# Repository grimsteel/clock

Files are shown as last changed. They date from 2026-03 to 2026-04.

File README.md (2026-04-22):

# Clock

> Working 4-person location clock. Uses Home Assistant location zone information.

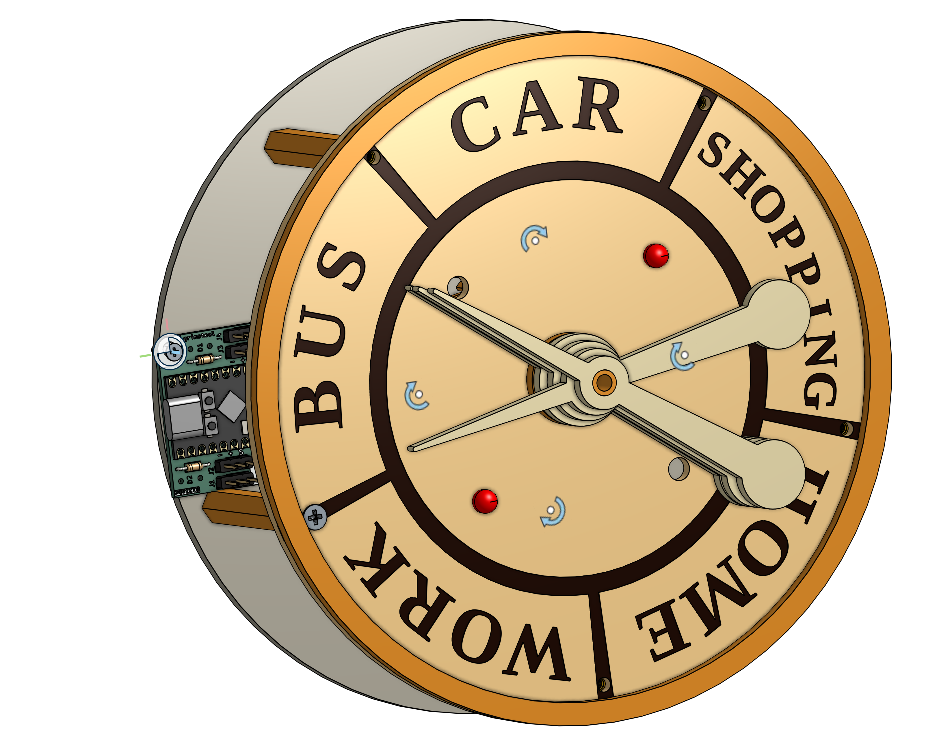
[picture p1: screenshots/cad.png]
CAD render


## Usage

### Assembly

1. 3D-print and laser cut the necessary components (see the `cad/` folder for a parts list and Onshape link)
2. Solder the ESP32 and pin headers onto the PCB.
3. Assemble the back frame (back, PCB, standoffs, and servo mount)
4. Attach the servos to the servo mount
5. Add the shafts, placing PTFE washers in between
6. Attach the front frame
7. Attach the front decorations and the hands

### Using it

8. Install one of the provided firmwares, configuring the people/locations as necessary (see `firmware/README.md`)
9. Profit. This does rely on accurate zone information in Home Assistant.

## Technical Information

### Structure

More information can be found in the `cad/` folder. The clock consists of a laser cut front and back frame.

Each hand is controlled by a servo with a 2:1 gear ratio. The servos and gears are mouted on a 3d-printed frame, which is fastened to the back frame.

The hands are attached to four concentric shafs, each terminating at a different height. This is part of the reason the clock is so thick.

The front includes 4 possible mounting spots for LEDs.

### PCB

The PCB consists of a surface mounted ESP32 C3 Supermini with connections for the 4 servos and 2 LEDs:

| Schematic | 3D render |
|---|---|
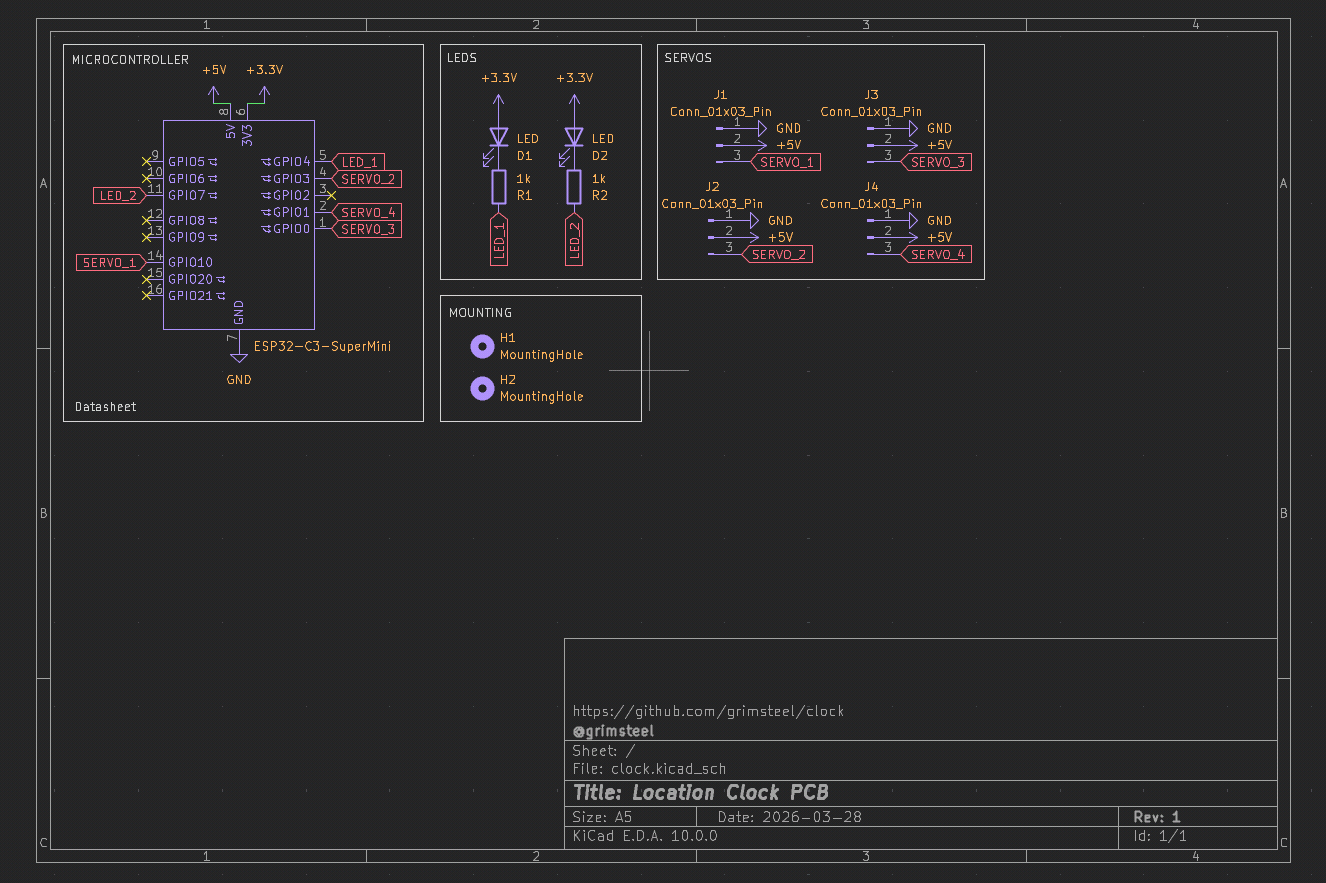
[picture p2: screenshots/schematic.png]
schematic
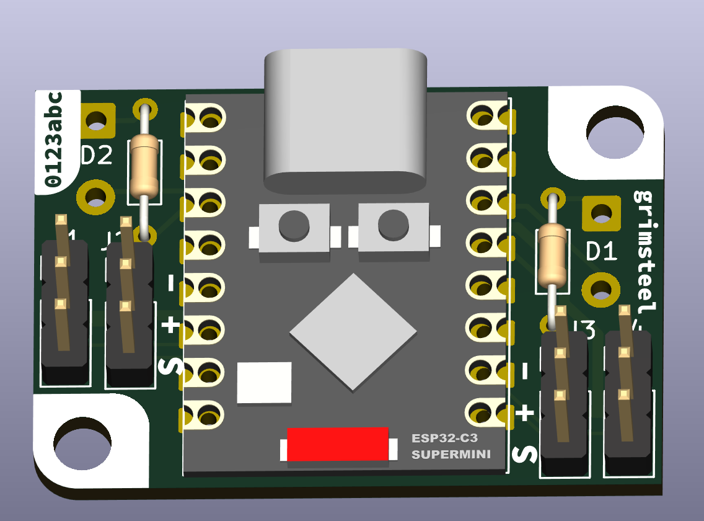
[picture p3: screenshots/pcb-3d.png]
3d
|  |   |
| Front | Back |
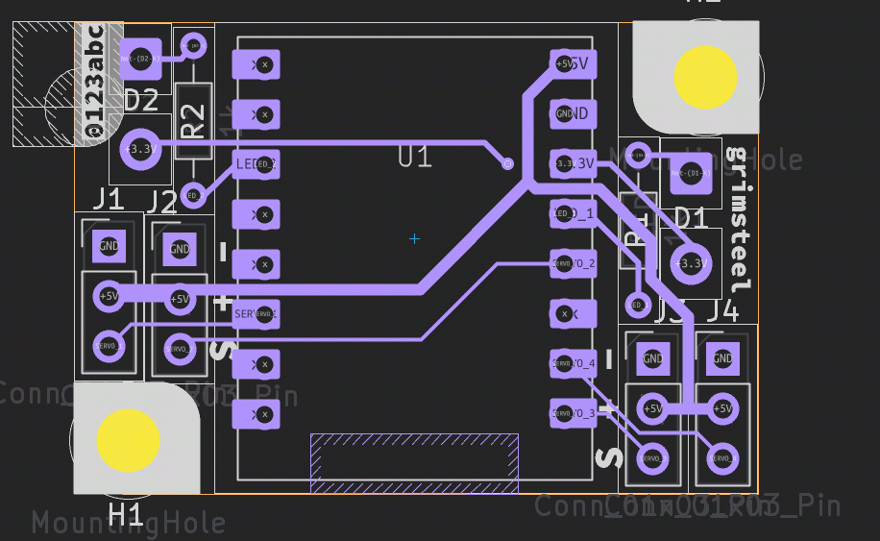
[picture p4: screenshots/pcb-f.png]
Front
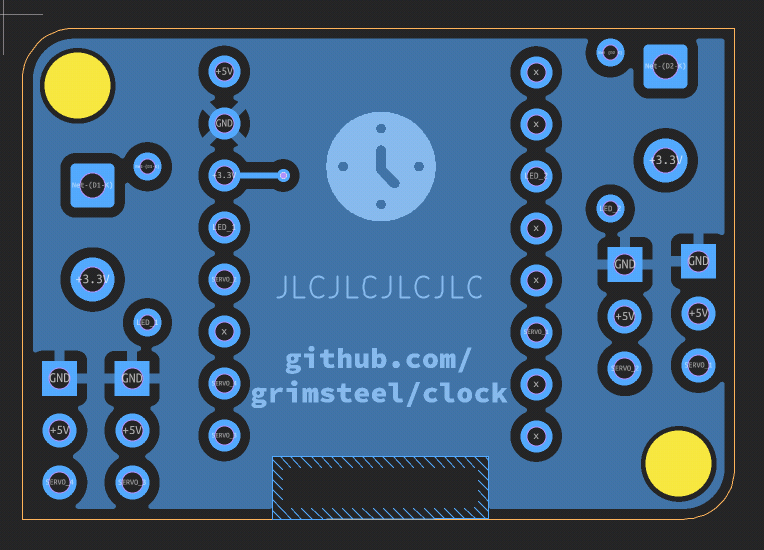
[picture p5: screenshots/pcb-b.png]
back
|  |  |

### Firmware

Two firmwares are provided: an ESPHome and a native ESP-IDF firmware. More information can be found in the `firmware/` folder.

## BOM

| Description | Link | Per-unit price | Quantity | Total price | Running price w/ tax |
|---|---|---|---|---|---|
| CAD components | https://cad.onshape.com/documents/5b8ef3e45edb03dc1124a4e9 | $0.00 | 1 | $0.00 | $0.00 |
| PCB | https://oshpark.com | $6.45 | 1 | $6.45 | $7.01 |
| ESP32-C3 Supermini | https://www.aliexpress.us/item/3256807292829704.html | $2.70 | 1 | $2.70 | $9.94 |
| MG90s Micro Servo (5 pack) | https://www.aliexpress.us/item/3256808303872992.html | $9.88 | 1 | $9.88 | $20.68 |

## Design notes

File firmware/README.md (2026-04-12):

# Clock Firmware

There are two options for the firmware for the clock: ESPHome and a native ESP-IDF firmware.

Both of these options require location zones to be set up in Home Assistant for the relevant locations. This results in the `person.person_1` sensors having a string value representing the zone.

## Usage (ESPHome)

The ESPHome firmware pulls location info for each person through the ESPHome Home Assistant API, using a Home Assistant text sensor.

In order to use it, you'll need to:
1. (Boilerplate) Update the ESPHome encryption key, OTA password, and fallback AP password
2. Update the entity IDs for the `person` text sensors. Person 1 corresponds to servo 1, and so on. The servo numbers match the PCB designators for the connectors (so, they're placed from left to right on the board.)
3. Update the mappings of location to section ID in `location_mappings.h`. The `default` case statement can be used for a catchall.

## Usage (Native)

The native firmware only communicates with an MQTT broker, so you'll need to configure Home Assistant to publish person location state over MQTT. This can be configured with [MQTT Statestream](https://www.home-assistant.io/integrations/mqtt_statestream/):

`configuration.yaml`:
```yaml
mqtt_statestream:
  base_topic: homeassistant
  # If you need to publish attributes for other things, I would recommend making template entities that just have the location zone info to avoid publishing location coordinates on MQTT.
  publish_attributes: false
  publish_timestamps: false
  include:
    entities:
      - person.person_1
      - person.person_2
      - person.person_3
      - person.person_4
```

The native firmware is likely more lightweight than the ESPHome firmware, and will be used if I make a battery-powered version in the future.

### Build instructions

In `firmware/native`:

1. Run `menuconfig` to configure the Wi-Fi and MQTT connection information:
   * `idf.py menuconfig`
   * These parameters are in the "Clock Connection Configuration" section
   * WPA2 and username/password MQTT can be configured here; for more advanced setups you'll need to edit `wifi.cpp`
2. Flash the firmware: `idf.py flash`
3. Upon running, the onboard LED will blink until the Wi-Fi and MQTT connections have been established.
4. A Home Assistant discovery payload will be published, so the MQTT items below can be controlled through Home Assistant:

### MQTT Protocol Specification

Topic prefix: `/devices/clock`
Availability: `/status` (either `on` or `off` (last will))

#### LEDs

The three LED IDs are `1`, `2`, and `board`. State values are either `on` or `off`.

State is published at `/leds/{led_id}/state`. They can be controlled at `/leds/{led_id}/control`. All LEDs are initially set to off upon connect.

#### Person Configuration

The four Home Assistant person IDs can be configured by writing to `/config/people`.

The value should be a comma separated list of person IDs, without the `person.` prefix:

`person_1,person_2,person_3,person_4`.

This value will be remembered in flash, so it only needs to be published once.

#### Location Configuration

The five location zone IDs can be configured by writing to `/config/locations`, in the same format as above.

This value will also be remembered. 

The actual sectors which each location corresponds to depends on the servo orientation

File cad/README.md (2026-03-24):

# CAD

[Onshape link](https://cad.onshape.com/documents/5b8ef3e45edb03dc1124a4e9/w/c25706113ef4329df2653fc9/e/a6187bd57ca36d70d5ce56bf)

## Parts List

| Part | Description | Quantity | Notes |
|---|---|---|---|
| Front | Clock face | 1 | Laser cut |
| Back | Clock back | 1 | Laser cut |
| DecorCenter | Center ring | 1 | 3dp, Optional |
| DecorEdge | Edge ring | 1 | 3dp, Optional |
| ServoMount | Servo and gear mount | 1 | 3dp |
| Standoff | Front/back separation | 5 | 3dp, print sideways |
| ServoGear | 40 tooth servo gear | 4 | 3dp, perimeters, high infill |
| Shaft{1,2,3,4} | 20 tooth gear and shaft | 4 | 3dp, perimeters, high infill |
| Arm{1,2,3,4} | Clock hand | 4 | Laser cut |

`assembly.step` holds the entire clock, with the servos and electronics.

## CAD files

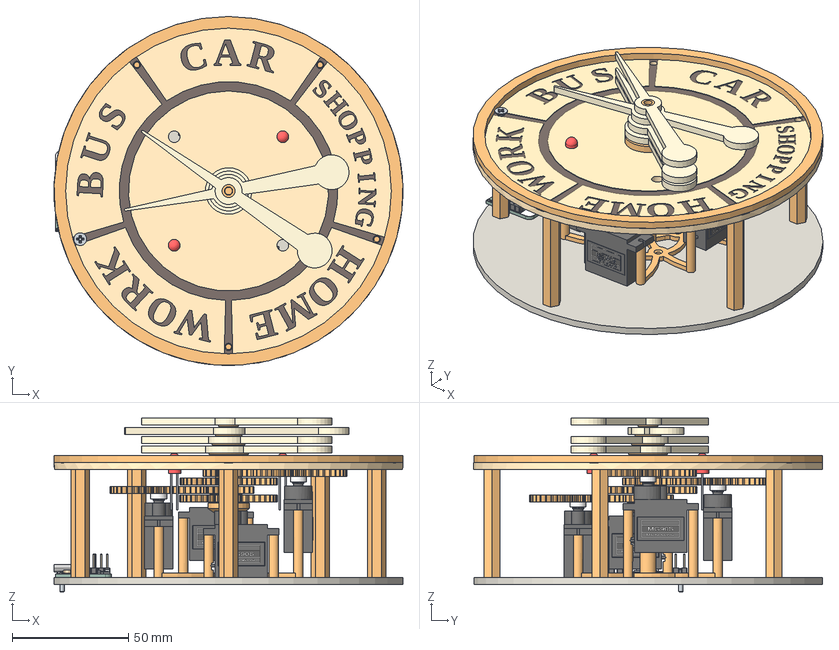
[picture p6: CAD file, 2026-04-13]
cad/assembly.step
150.0 x 150.0 x 74.7 mm
Shaft x 4
Arm x 4
PH Countersunk flat head screw M2x0.4 x 10
CenterAxle
DecorCenter
Front
DecorEdge
Back
Standoff x 5
M3x5.74-Insert x 10
Spur gear (40 teeth) x 4
Half Servo Horn x 4
etiquette001 x 4
Tube x 4
Tube002 x 4
Cylindre001 x 4
Cylindre002 x 4
Tube001 x 4
base001 x 4
axe x 4
etiquette x 4
Cylindre x 4
PH Countersunk flat head screw M3x0.5 x 10
clock_silkscreen x 91
PinHeader_1x03_P2.54mm_Vertical x 4
clock_PCB
R_Axial_DIN0204_L3.6mm_D1.6mm_P7.62mm_Horizontal x 2

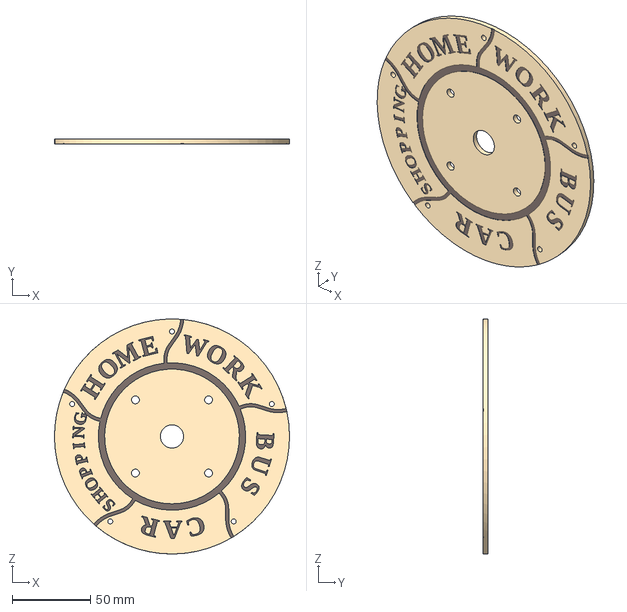
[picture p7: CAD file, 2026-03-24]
cad/front.step
150.0 x 3.00 x 150.0 mm

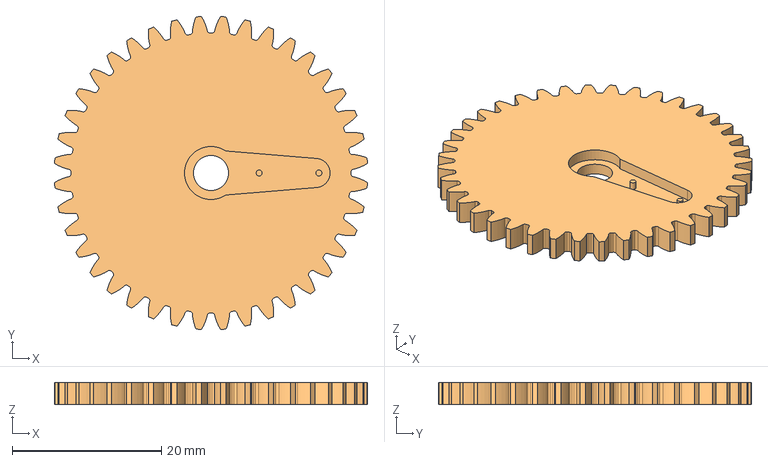
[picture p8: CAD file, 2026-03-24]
cad/servo-gear.step
41.9 x 41.9 x 3.00 mm

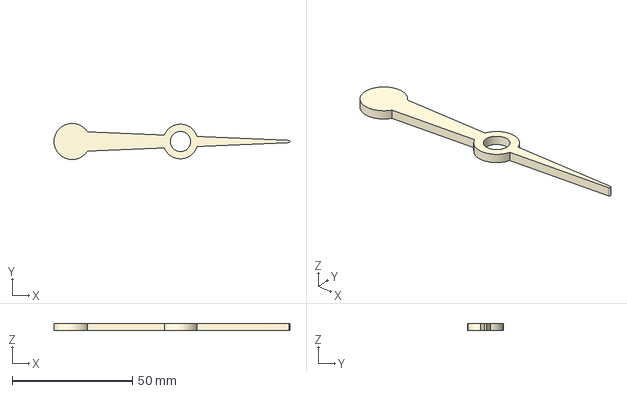
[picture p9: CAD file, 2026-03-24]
cad/arm-3.step
98.0 x 15.0 x 3.00 mm

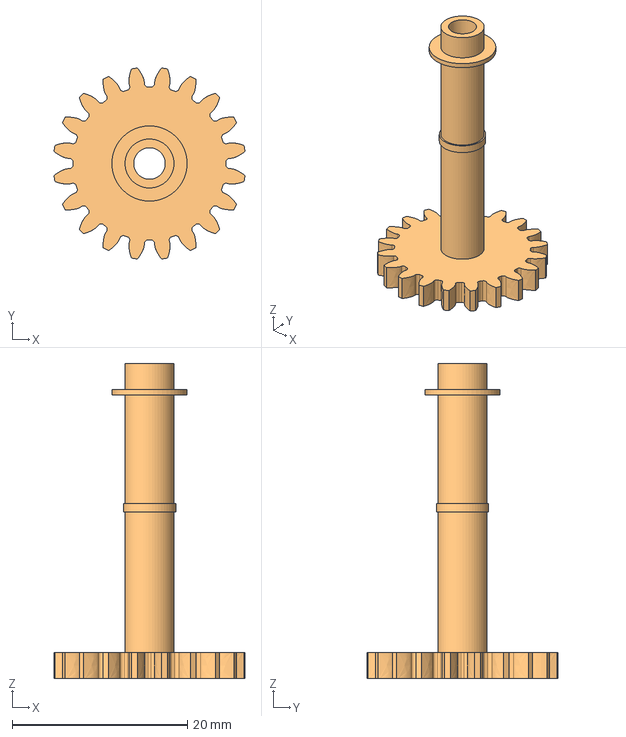
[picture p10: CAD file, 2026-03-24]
cad/shaft-4.step
21.8 x 21.8 x 36.0 mm

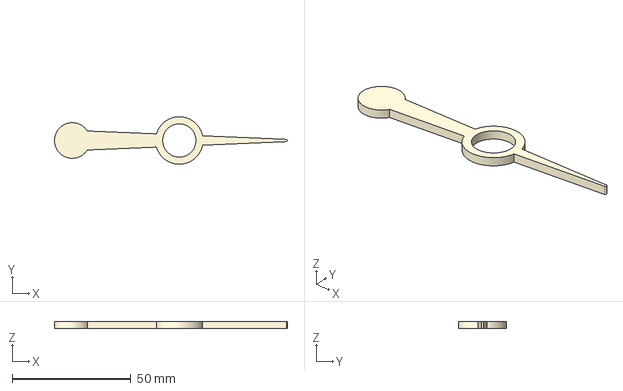
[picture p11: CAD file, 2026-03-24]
cad/arm-1.step
98.0 x 20.0 x 3.00 mm

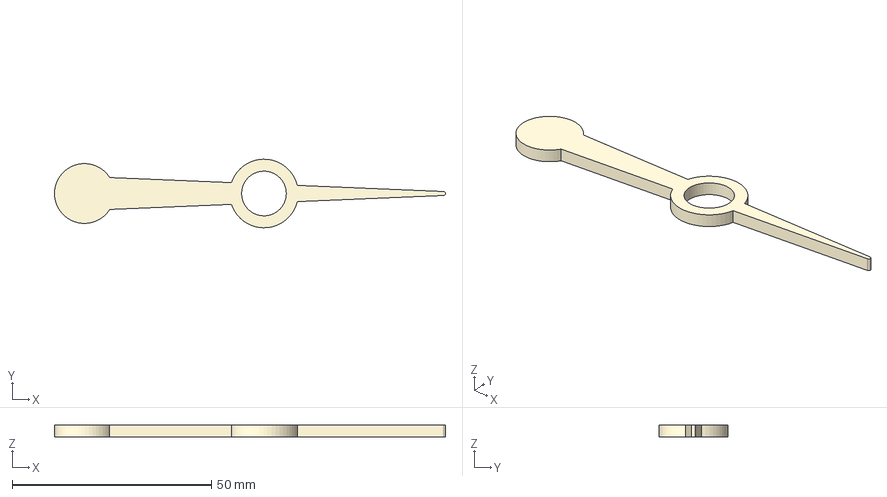
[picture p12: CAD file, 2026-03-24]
cad/arm-2.step
98.0 x 17.2 x 3.00 mm

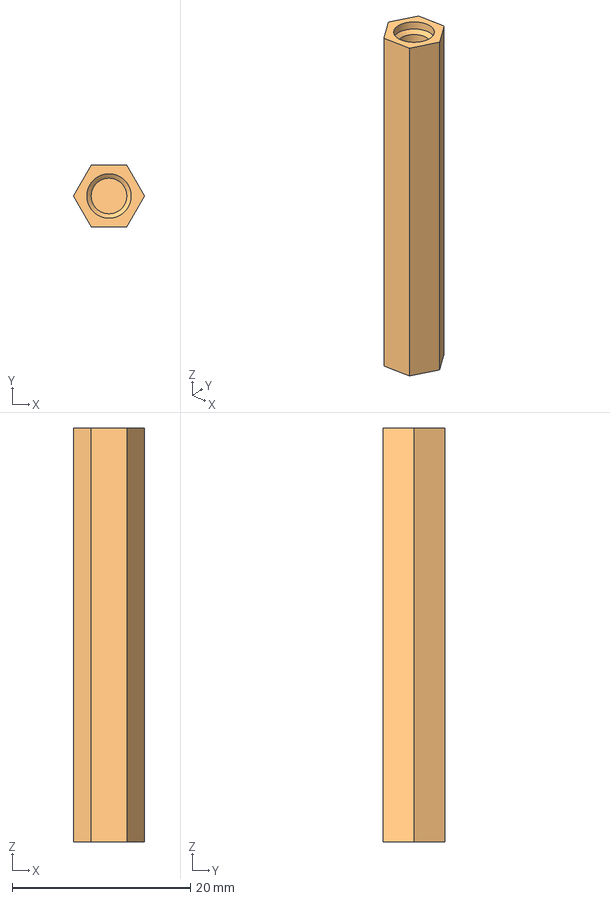
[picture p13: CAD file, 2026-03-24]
cad/standoff.step
8.00 x 6.93 x 46.5 mm

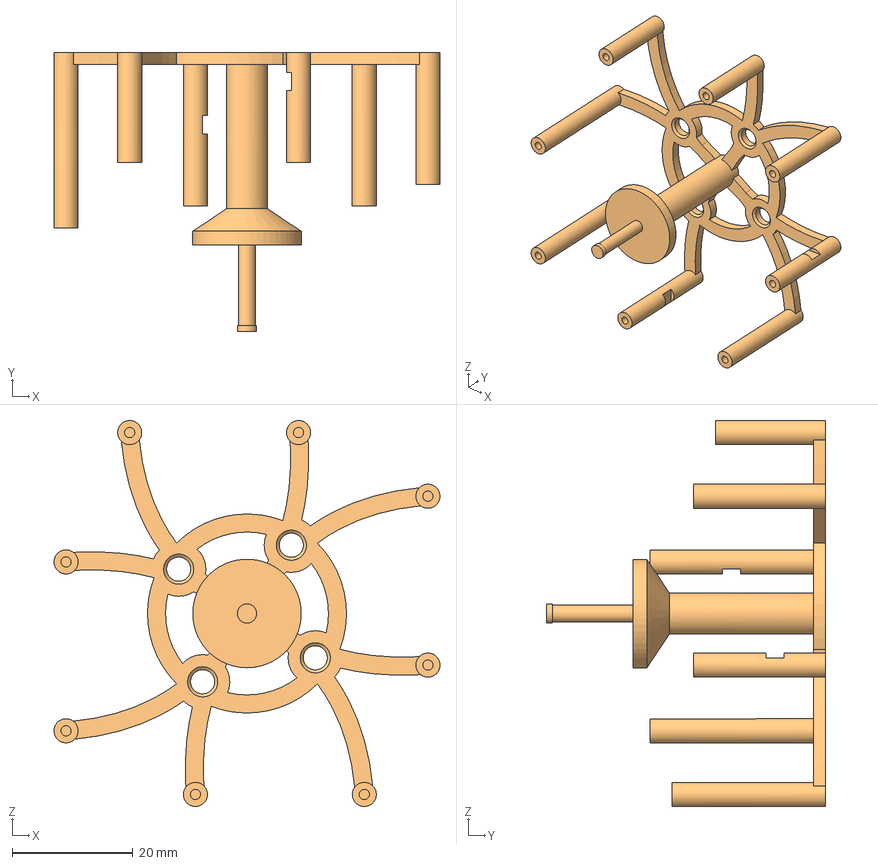
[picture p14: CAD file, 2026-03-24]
cad/center-axle.step
64.0 x 46.3 x 64.0 mm

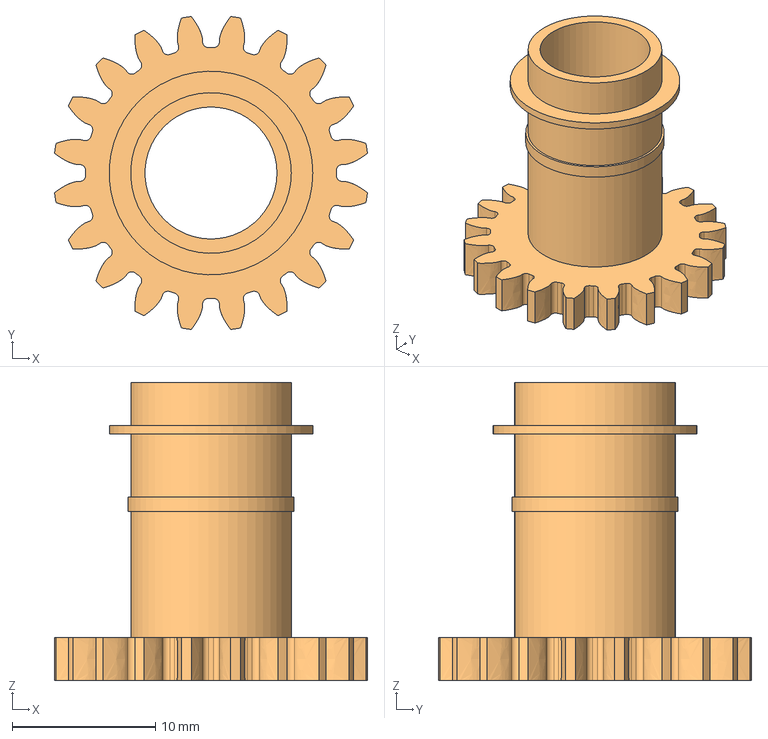
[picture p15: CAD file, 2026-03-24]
cad/shaft-2.step
21.8 x 21.8 x 20.8 mm

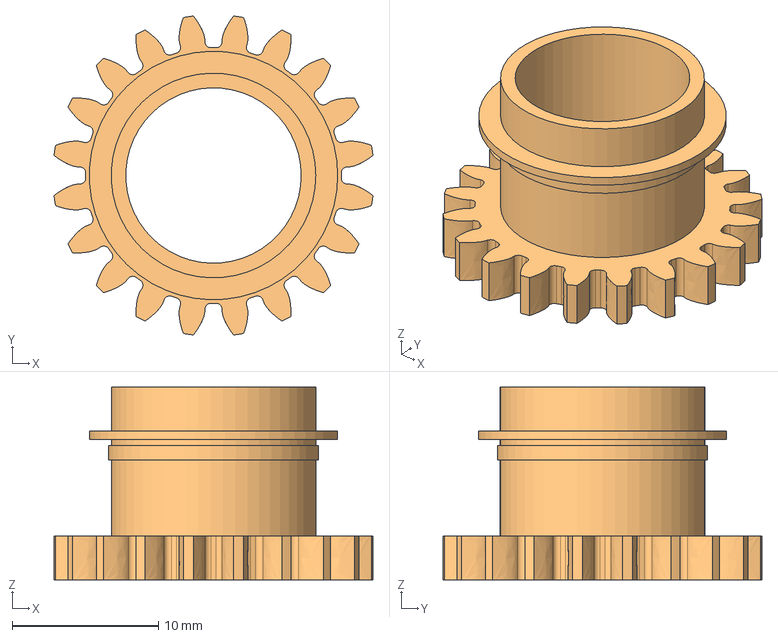
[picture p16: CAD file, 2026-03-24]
cad/shaft-1.step
21.8 x 21.8 x 13.2 mm

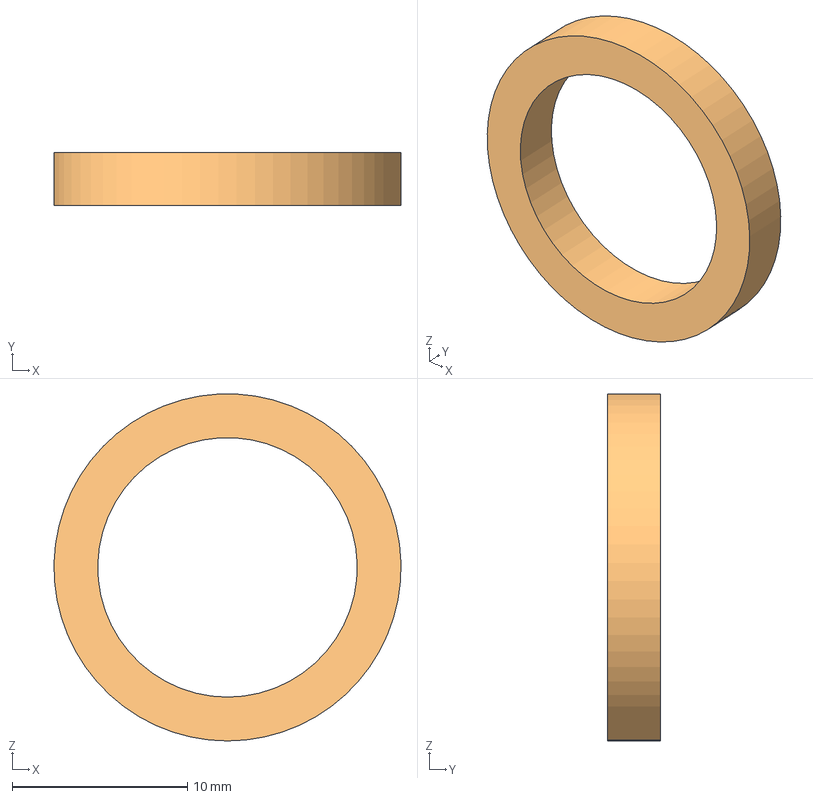
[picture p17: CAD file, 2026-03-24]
cad/decor-center.step
19.8 x 3.00 x 19.8 mm

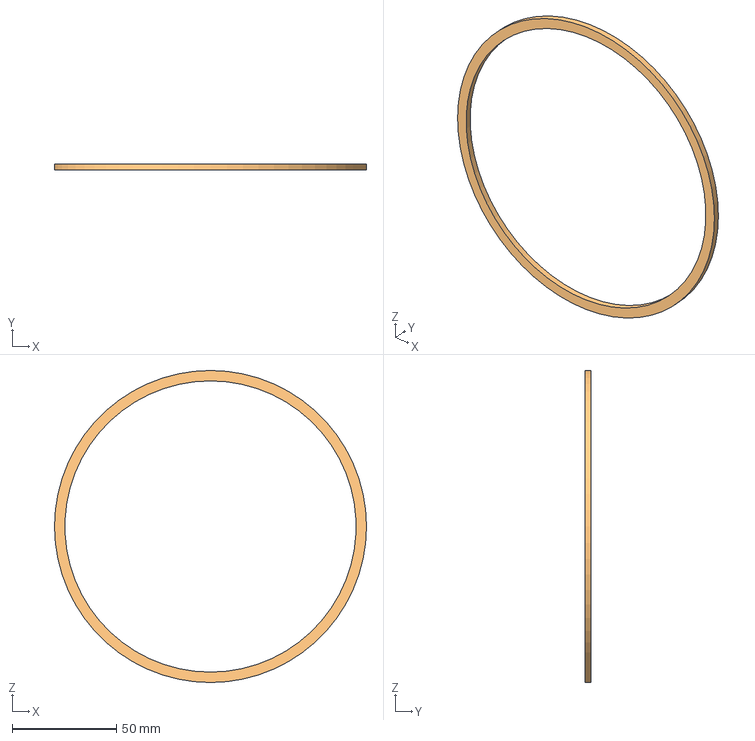
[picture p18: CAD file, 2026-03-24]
cad/decor-edge.step
150.0 x 3.00 x 150.0 mm

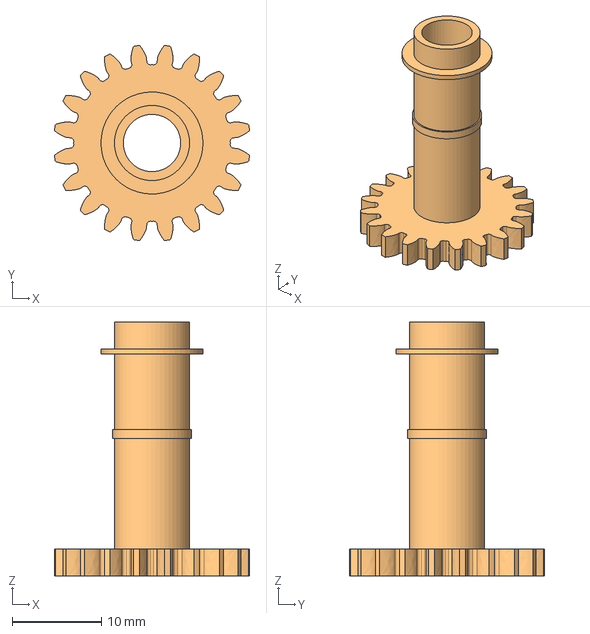
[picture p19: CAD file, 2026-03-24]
cad/shaft-3.step
21.8 x 21.8 x 28.4 mm

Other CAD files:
cad/back.step
cad/arm-4.step

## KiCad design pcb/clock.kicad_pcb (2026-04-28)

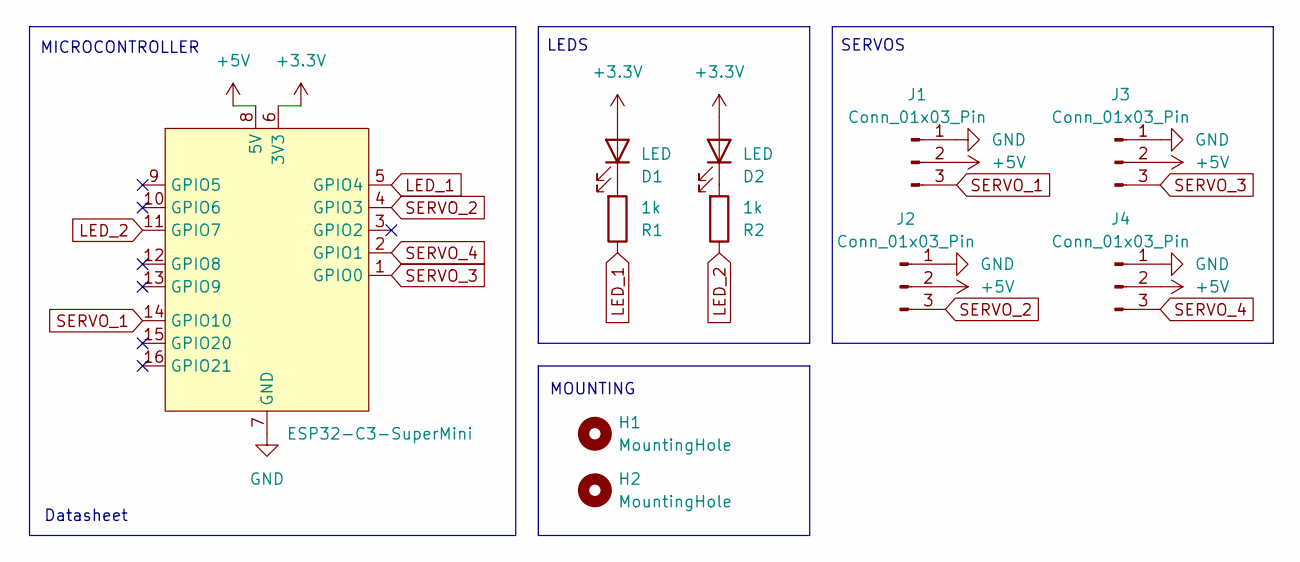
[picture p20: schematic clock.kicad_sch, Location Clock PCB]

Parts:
D1, D2: LED; SolderWire-0.5sqmm_1x02_P4.6mm_D0.9mm_OD2.1mm
H1, H2: MountingHole; MountingHole_3.2mm_M3
J1, J2, J3, J4: Conn_01x03_Pin; PinHeader_1x03_P2.54mm_Vertical
R1, R2: 1k; R_Axial_DIN0204_L3.6mm_D1.6mm_P7.62mm_Horizontal
U1: ESP32-C3-SuperMini

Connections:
+3.3V: D1.2 (A), D2.2 (A), U1.6 (3V3)
+5V: J1.2, J2.2, J3.2, J4.2, U1.8 (5V)
GND: J1.1, J2.1, J3.1, J4.1, U1.7 (GND)
LED_1: R1.1, U1.5 (GPIO4)
LED_2: R2.1, U1.11 (GPIO7)
unnamed: D1.1 (K), R1.2
unnamed: D2.1 (K), R2.2
SERVO_1: J1.3, U1.14 (GPIO10)
SERVO_2: J2.3, U1.4 (GPIO3)
SERVO_3: J3.3, U1.1 (GPIO0)
SERVO_4: J4.3, U1.2 (GPIO1)

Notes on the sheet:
MOUNTING
MICROCONTROLLER
LEDS
Datasheet
SERVOS

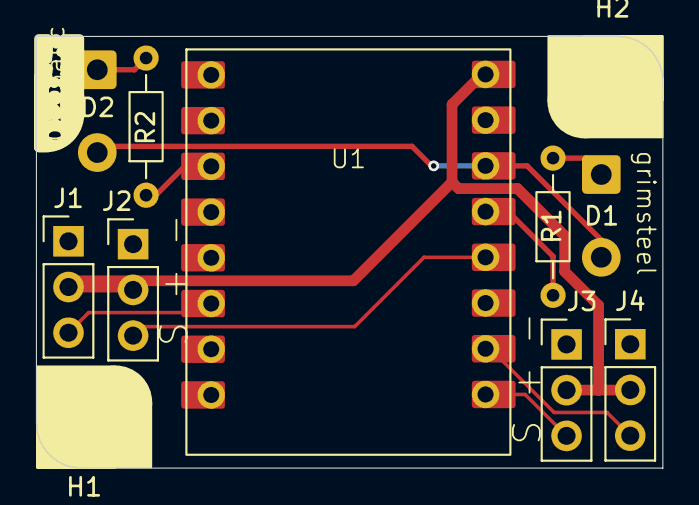
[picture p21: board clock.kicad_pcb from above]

Board: 2 copper layers, 34.8 x 24.0 mm, 11 parts (0 on the bottom side), 11 nets.

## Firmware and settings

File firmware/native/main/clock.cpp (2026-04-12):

#include "esp_event_cxx.hpp"
#include "esp_exception.hpp"
#include "esp_log.h"
#include "esp_mqtt_client_config.hpp"
#include "freertos/idf_additions.h"
#include "gpio_cxx.hpp"
#include "portmacro.h"
#include "sdkconfig.h"
#include "wifi.hpp"
#include "mqtt.hpp"
#include "servo.cpp"
#include "esp_event.h"
#include "nvs_flash.h"
#include "nvs.h"
#include "nvs_handle.hpp"
#include <vector>

#define TAG "clock"

// lets encrypt
extern const char isrgrootx1_pem_start[]   asm("_binary_isrgrootx1_pem_start");
extern const char isrgrootx1_pem_end[]   asm("_binary_isrgrootx1_pem_end");

class ClockManager {
public:
    ClockManager(idf::event::ESPEventLoop &loop) : event_loop(loop) {
        // Initialize NVS
        esp_err_t err = nvs_flash_init();
        if (err == ESP_ERR_NVS_NO_FREE_PAGES || err == ESP_ERR_NVS_NEW_VERSION_FOUND) {
            // NVS partition was truncated and needs to be erased
            // Retry nvs_flash_init
            ESP_ERROR_CHECK(nvs_flash_erase());
            err = nvs_flash_init();
        }
        ESP_ERROR_CHECK( err );
        nvs_handle = nvs::open_nvs_handle("storage", NVS_READWRITE, &err);
        ESP_ERROR_CHECK(err);
        
        // Fetch from nvs
        char zone_str[7] = "zone_0";
        for (int i = 0; i < 5; i++) {
            // build actual string
            zone_str[5] = '0' + i;
            zones[i] = nvs_get_string(zone_str);
        }
        char people_str[9] = "person_0";
        for (int i = 0; i < 4; i++) {
            // build actual string
            people_str[7] = '0' + i;
            people[i] = nvs_get_string(people_str);
        }
        
        // Init servos
        servo::Servo::init();
        servos.reserve(4);
        for (int i = 0; i < 4; i++) {
            servos.push_back(servo::Servo(servo_gpios[i]));
        }
    }
    
    void init_callbacks() {
        event_loop.register_event(mqtt::ClockMQTTClient::MQTT_EVENT_LOCATIONS, [this](const idf::event::ESPEvent& event, void* data) {
            mqtt::LocationEventPayload* payload = static_cast<mqtt::LocationEventPayload*>(data);
            char zone_str[7] = "zone_0";
            for (int i = 0; i < 5; i++) {
                // build actual string
                zone_str[5] = '0' + i;
                zones[i] = move(payload->locations[i]);
                nvs_handle->set_string(zone_str, zones[i].c_str());
                nvs_handle->commit();
            }
        });
        event_loop.register_event(mqtt::ClockMQTTClient::MQTT_EVENT_PEOPLE, [this](const idf::event::ESPEvent& event, void* data) {
            mqtt::PeopleEventPayload* payload = static_cast<mqtt::PeopleEventPayload*>(data);
            char people_str[9] = "person_0";
            for (int i = 0; i < 4; i++) {
                // build actual string
                people_str[7] = '0' + i;
                people[i] = move(payload->people[i]);
                nvs_handle->set_string(people_str, people[i].c_str());
                nvs_handle->commit();
            }
        });
        event_loop.register_event(mqtt::ClockMQTTClient::MQTT_EVENT_LOCATION_UPDATE, [this](const idf::event::ESPEvent& event, void* data) {
            mqtt::LocationUpdateEventPayload* payload = static_cast<mqtt::LocationUpdateEventPayload*>(data);
            int person_idx = -1, location_idx = -1;
            // Find index
            for (int i = 0; i < 5; i++) {
                if (zones[i] == payload->location) {
                    location_idx = i;
                    break;
                }
            }
            for (int i = 0; i < 4; i++) {
                if (people[i] == payload->person) {
                    person_idx = i;
                    break;
                }
            }
            if (person_idx == -1 || location_idx == -1) return;
            // scale to full 360, then move by person, then move to center
            int angle = location_idx * 360 / 5 + person_idx * 360 / (5 * 4) + 360 / (5 * 4 * 2);
            servos[person_idx].set_angle(angle);
        });
    }
private:
    std::string nvs_get_string(const char* key) {
        size_t str_size;
        esp_err_t err = nvs_handle->get_item_size(nvs::ItemType::SZ, key, str_size);
        std::string str;
        if (err != ESP_ERR_NVS_NOT_FOUND) {
            str.resize(str_size); // size includes null term
            nvs_handle->get_string(key, str.data(), str_size);
        }
        
        return str;
    }
    std::unique_ptr<nvs::NVSHandle> nvs_handle;
    idf::event::ESPEventLoop &event_loop;
    std::string zones[5];
    std::string people[4];
    std::vector<servo::Servo> servos;
    idf::GPIONum servo_gpios[4] = { idf::GPIONum(10), idf::GPIONum(3), idf::GPIONum(0), idf::GPIONum(1) };
};

extern "C" void app_main(void)
{
    try {
        ESP_LOGI(TAG, "Initializing...");
        
        const idf::GPIO_Output led_1(idf::GPIONum(4));
        const idf::GPIO_Output led_2(idf::GPIONum(7));
        const idf::GPIO_Output led_onboard(idf::GPIONum(8));
        
        static idf::event::ESPEventLoop loop;
        
        // off
        led_1.set_high();
        led_2.set_high();
        
        // turn status led on until connect
        led_onboard.set_low();
        
        static ClockManager manager(loop);
        
        ESP_LOGI(TAG, "Initialized peripherals");
        
        wifi::connect();
        
        ESP_LOGI(TAG, "Connected to Wi-Fi");
        
        // init MQTT
        idf::mqtt::BrokerConfiguration broker {
            .address = {idf::mqtt::URI{std::string{CONFIG_CLOCK_MQTT_BROKER}}},
            .security = idf::mqtt::CryptographicInformation{idf::mqtt::PEM{isrgrootx1_pem_start}}
        };
        idf::mqtt::ClientCredentials credentials {
            .username = std::string { CONFIG_CLOCK_MQTT_USERNAME },
            .authentication = idf::mqtt::Password { std::string { CONFIG_CLOCK_MQTT_PASSWORD } }
        };

        mqtt::ClockMQTTClient mqtt_client(broker, credentials, loop);
        
        ESP_LOGI(TAG, "Connected to MQTT broker");
        
        // events are handled in the event loop
        manager.init_callbacks();
        while (true) vTaskDelay(portMAX_DELAY);
    } catch (idf::GPIOException &e) {
        ESP_LOGE(TAG, "GPIO exception: %s", esp_err_to_name(e.error));
    } catch (wifi::WifiException &e) {
        ESP_LOGE(TAG, "Wi-Fi exception: %s", esp_err_to_name(e.error));
    } catch (idf::ESPException &e) {
        ESP_LOGE(TAG, "Miscellaneous exception: %s", esp_err_to_name(e.error));
    }
}

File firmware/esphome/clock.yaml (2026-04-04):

# ESPHome base config

esphome:
  name: presence_clock
  friendly_name: Presence Clock
  includes:
    - location_mappings.h

esp32:
  variant: esp32c3
  framework:
    type: esp-idf

logger:

api:
  encryption:
    key: ""

ota:
  - platform: esphome
    password: ""

wifi:
  ssid: !secret wifi_ssid
  password: !secret wifi_password
  domain: ".local"
  use_address: ""

  ap:
    ssid: "Clock Fallback Hotspot"
    password: ""

captive_portal:

# Clock-specific config

text_sensor:
  - platform: homeassistant
    id: person_1
    entity_id: person.person_1
    on_value:
      then:
        - script.execute: apply_locations
  - platform: homeassistant
    id: person_2
    entity_id: person.person_2
    on_value:
      then:
        - script.execute: apply_locations
  - platform: homeassistant
    id: person_3
    entity_id: person.person_3
    on_value:
      then:
        - script.execute: apply_locations
  - platform: homeassistant
    id: person_4
    entity_id: person.person_4
    on_value:
      then:
        - script.execute: apply_locations

output:
  # LEDs
  - platform: gpio
    pin: GPIO4
    id: light_left
    inverted: true
  - platform: gpio
    pin: GPIO7
    id: light_right
    inverted: true
  # Servos
  - platform: ledc
    pin: GPIO10
    frequency: "50Hz"
    id: servo_out_1
  - platform: ledc
    pin: GPIO3
    frequency: "50Hz"
    id: servo_out_2
  - platform: ledc
    pin: GPIO0
    frequency: "50Hz"
    id: servo_out_3
  - platform: ledc
    pin: GPIO1
    frequency: "50Hz"
    id: servo_out_4

light:
  - platform: status_led
    name: "Onboard LED"
    pin:
      number: GPIO8
      inverted: true
  - platform: binary
    output: light_left
    name: "Left LED"
  - platform: binary
    output: light_right
    name: "Right LED"

servo:
  - id: servo_1
    output: servo_out_1
  - id: servo_2
    output: servo_out_2
  - id: servo_3
    output: servo_out_3
  - id: servo_4
    output: servo_out_4

script:
  - id: apply_locations
    # if a location update happens while this is running, just restart the script
    mode: restart
    then:
      - lambda: |-
          string loc_states_str[] = {
            id(person_1).state,
            id(person_2).state,
            id(person_3).state,
            id(person_4).state
          };
          int loc_states[4];
          double servo_states[4];
          // parse location string into int (see external header file)
          for (int i = 0; i < 4; i++) loc_states[i] = location_int(loc_states_str[i]);
          
          int sector_size = 360 / 5; // 5 locs
          // each hand has its own subsector to avoid overlap
          int subsector_size = sector_size / 4;
          
          for (int i = 0; i < 4; i++) {
             // convert [0, 5) to [0, 360)
             loc_states[i] *= sector_size;
             // hand offset
             loc_states[i] += subsector_size * i;
             // put in middle
             loc_states[i] += subsector_size / 2;
             // map to [-1, 1]
             servo_states[i] = (loc_states[i] - 180) / 180.0;
          }
          id(servo_1).write(servo_states[0]);
          id(servo_2).write(servo_states[1]);
          id(servo_3).write(servo_states[2]);
          id(servo_4).write(servo_states[3]);
          

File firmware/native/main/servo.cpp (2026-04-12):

#include "servo.hpp"
#include "driver/ledc.h"
#include "hal/ledc_types.h"

namespace servo {
// Helper macro to throw an esp_err_t as a ServoException
#define SERVO_CHECK_THROW(err) \
    do {                                                                         \
    esp_err_t result = (err);                                                  \
    if (result != ESP_OK)                                                      \
        throw ServoException(result);                                             \
    } while (0)
    
#define DUTY_CYCLE_FULL (8192 / 5) // 2^13 / 5
    
void Servo::init() {
    ledc_timer_config_t ledc_timer = {};
    ledc_timer.speed_mode = LEDC_LOW_SPEED_MODE;
    ledc_timer.duty_resolution = LEDC_TIMER_13_BIT;
    ledc_timer.timer_num = LEDC_TIMER_0;
    ledc_timer.freq_hz = SERVO_PWM_FREQUENCY;
    ledc_timer.clk_cfg = LEDC_AUTO_CLK;
    SERVO_CHECK_THROW(ledc_timer_config(&ledc_timer));
}

// static counter
ledc_channel_t Servo::current_channel_id = LEDC_CHANNEL_0;

Servo::Servo(idf::GPIONum gpio_num) {
    channel_id = Servo::current_channel_id;
    // increment
    Servo::current_channel_id = static_cast<ledc_channel_t>(static_cast<int>(Servo::current_channel_id) + 1);
    
    ledc_channel_config_t ledc_channel = {};
    ledc_channel.gpio_num       = (int) gpio_num.get_value();
    ledc_channel.speed_mode     = LEDC_LOW_SPEED_MODE;
    ledc_channel.channel        = channel_id;
    ledc_channel.timer_sel      = LEDC_TIMER_0;
    ledc_channel.duty           = DUTY_CYCLE_FULL; // 5% = 0 deg
    ledc_channel.hpoint         = 0;
    SERVO_CHECK_THROW(ledc_channel_config(&ledc_channel));
}

void Servo::set_angle(int angle) {
    if (angle < 0 || angle >= 360) return;
    // fraction of 1/5
    uint32_t duty_fraction = DUTY_CYCLE_FULL * 360 / angle;
    // need to vary from 1/5 to 2/5
    duty_fraction += DUTY_CYCLE_FULL;
    SERVO_CHECK_THROW(ledc_set_duty(LEDC_LOW_SPEED_MODE, channel_id, duty_fraction));
    // Update duty to apply the new value
    SERVO_CHECK_THROW(ledc_update_duty(LEDC_LOW_SPEED_MODE, channel_id));
}

}

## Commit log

2026-03-24 cad: initial complete clock cad
    [arm-1.step, arm-2.step, arm-3.step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]
2026-03-29 pcb: finish v1 schematic, pcb
    [clock.kicad_pcb, clock.kicad_sch]
2026-04-04 pcb: led improvements
    [clock.kicad_pcb, clock.kicad_sch]
2026-04-04 firmware: add esphome firmware
    [clock.kicad_pcb, clock.kicad_sch]
2026-04-12 finish native firmware: mqtt, servos, event loop
2026-04-13 docs: finish readme, add screenshots and prod files
    [assembly.step, bom.csv, clock.kicad_pcb]
2026-04-22 bom: update links
    [bom.csv]
2026-04-28 pcb: remove jlc serial
    [clock.kicad_pcb]
